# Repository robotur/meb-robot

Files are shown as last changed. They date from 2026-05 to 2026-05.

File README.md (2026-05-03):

# meb-robot
Retrospective documentation of a Maze Solver robot made for MEB ROBO 2025 &amp; 2026

This is a compact, autonomous maze solver robot. Made with a 3d printed chassis and IR sensors; was designed and iterated over the span of 2 years to optimize turning and wall following ability.

 * Microcontroller: Arduino Nano
 * Sensors: 3x MR 45-5V diffuse IR sensors
 * Custom 3D printed PETG
 * Logic: Wall following (Left side)
   
[Watch the video](https://youtu.be/hQ72KUeb8lM)

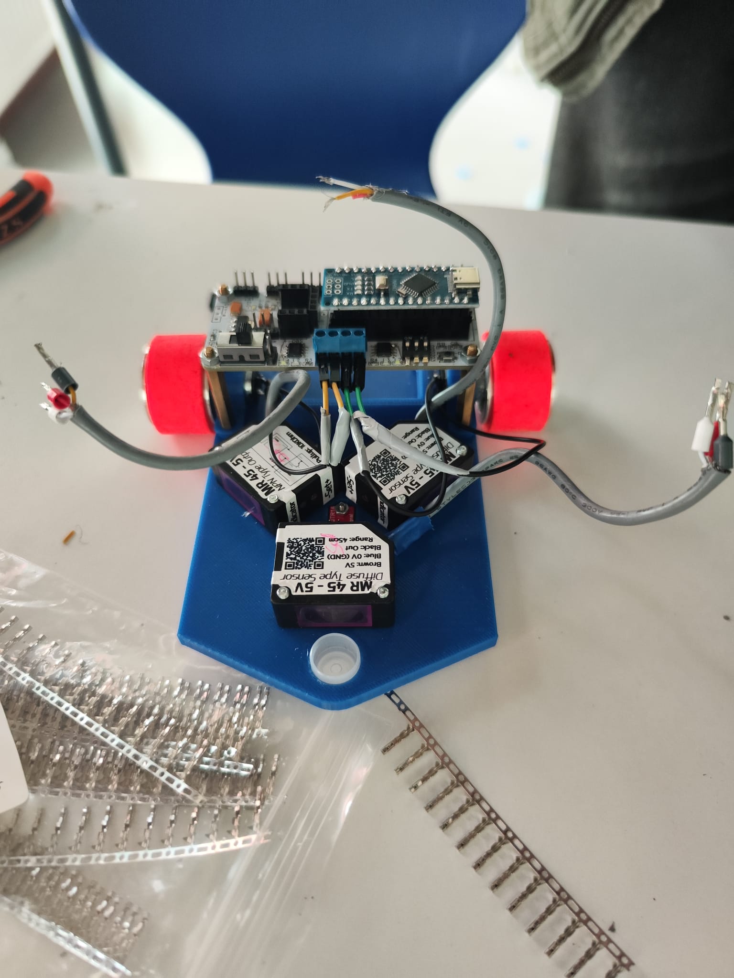
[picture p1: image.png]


# Engineering Decisions
Optimized sensor array for navigation:
 * used 3 point diffuse sensor array (45 degree angle to each side)
 * the 45 degree angle allows the sensors to detect the wall earlier allowing for smoother velocity transitions and preventing stuttering in logic

Finish detection:
 * used a compact QTR type IR sensor that faces the ground with a small mounting point in an accessible location in the middle of the chassis
 * this allows for a digital output signal showing whether the color of the ground is reflective or not (Effectively black/white) and thus allows me to find the differently colored finish grid

Inverted motor mount:
 * I mounted the motors on the top side of the chassis plate rather than the bottom
 * This lowers the entire chassis to the ground, lower CoM reduces the moment of inertia in high speed turns, massively decreasing the force that tips the robot/prevents it from losing traction

# Mentorship & Leadership
After a relatively successful 2025 season with 10 students (5 teams), there were a lot of interested students. I co-led the technical mentorship for 8 incoming Preparatory and 9th grade students.
I translated my 2025 and 2026 experience into a 'base model' (this repo) and i hope to enable new students and current participants to move past basic assembly and focus on more advanced logic and troubleshooting

 * Design and manufacturing: I handled the full CAD to print cycle, ensuring every team had a structurally sound chassis
 * Component Integration: I pre-selected the sensor array and motor positions to eliminate hardware level issues, allowing the students to focus on logic
 * Technical Direction: I gave them a guide to follow for connecting electronics components for optimal IO and logic management

By abstracting mechanical complexity I allowed the 8 junior students to engage directly with logic; turning raw signals into autonomous behavior through their own code.

# 2025-2026 Iteration Comparison
In the 2025 version, the motors were at the bottom of the plate. This meant the robot sat higher off the ground compared to other robots but also meant that because the caster wheel was shorter than the height of the chassis plate from the ground, it made the entire robot stand on a 15 degree angle which ruined the sensors' output because the sensors were effectively looking at the ground instead of forward.

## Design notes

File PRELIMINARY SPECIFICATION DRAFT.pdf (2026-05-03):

PRELIMINARY SPECIFICATION DRAFT

Challenge: During the integration phase, there was a hardware bottleneck. The three directional sensors and underside sensor and the motor drivers exhausted all available digital IO pins on the arduino nano.

Solution: I researched the ATmega328P silicon architecture and confirmed that pins A0 through A5 are internally mapped and can be addressed as digital pins using the “pinMode()” and “digitalRead()” functions

I instructed the students to solder 12 header pins (arranged in 4 signal-power-ground groups) onto the prototype shield, specifically utilizing the analog rail for digital input and pins for easy replacement incase of sensor failure

I guided the students through updating their code logic to treat A1-A5 as digital triggers successfully expanding our sensor capacity without needing a larger microcontroller

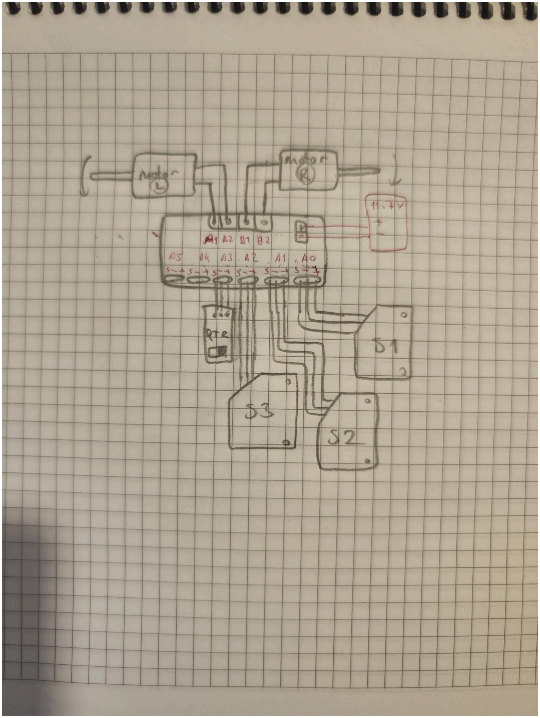
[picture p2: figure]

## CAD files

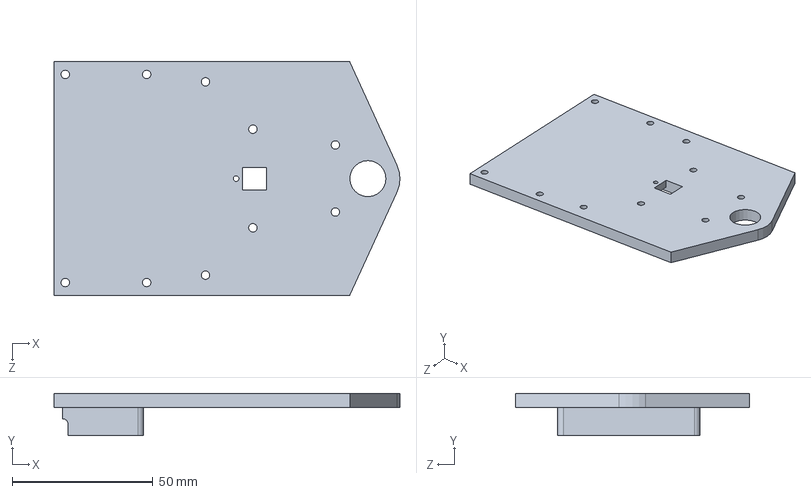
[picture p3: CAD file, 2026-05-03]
CAD/plate.SLDPRT
122.8 x 15.0 x 82.9 mm

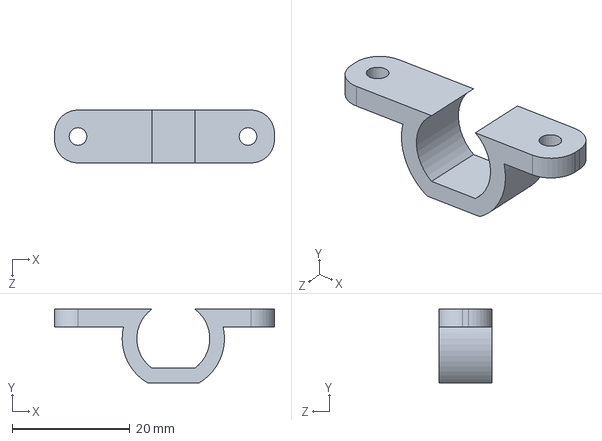
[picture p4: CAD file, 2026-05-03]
CAD/motor_holder.SLDPRT
37.4 x 12.5 x 9.00 mm

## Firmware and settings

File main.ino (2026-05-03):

// --- Hız Tanımlamaları ---
constexpr uint8_t DEFAULT_SPEED = 150;
constexpr uint8_t TURN_SPEED    = 100; 

// --- Motor Pin Tanımlamaları (T4950) ---
#define l_e_f_t_m_1 10
#define l_e_f_t_m_2 6
#define r_i_g_h_t_m_1 5
#define r_i_g_h_t_m_2 4

// --- MR45 Sensör Pinleri ---
#define SAG_SENSOR A1
#define SOL_SENSOR A3
#define ON_SENSOR  A2

void setup() {
  pinMode(l_e_f_t_m_1, OUTPUT);
  pinMode(l_e_f_t_m_2, OUTPUT);
  pinMode(r_i_g_h_t_m_1, OUTPUT);
  pinMode(r_i_g_h_t_m_2, OUTPUT);
  
  // MR45 Dijital veri gönderdiği için INPUT_PULLUP daha sağlıklı olabilir
  pinMode(SAG_SENSOR, INPUT);
  pinMode(SOL_SENSOR, INPUT);
  pinMode(ON_SENSOR,  INPUT);
}

void loop() {
  /* 
     MR45 MANTIĞI: 
     digitalRead == 0 -> ENGEL VAR
     digitalRead == 1 -> YOL BOŞ
  */
  bool solBos = digitalRead(SOL_SENSOR) == HIGH;
  bool onBos  = digitalRead(ON_SENSOR)  == HIGH;
  bool sagBos = digitalRead(SAG_SENSOR) == HIGH;

  // --- SOL ÖNCELİKLİ (Left Hand on Wall) ALGORİTMASI ---
  
  if (solBos) {
    // Solun boş olması en yüksek öncelik. 
    // Hafif ileri gidip öyle dönmek robotun duvara çarpmasını engeller.
    dur(); 
    delay(350); 
    solaDon();
    delay(200); // 90 derece tam dönene kadar ayarla
    ileriGit();
    delay(135);
  } 
  else if (onBos) {
    // Sol kapalıysa ama önün açıksa dümdüz devam et
    ileriGit();
  } 
  else if (sagBos) {
    // Sol ve ön kapalıysa sağa dön
    dur();
    delay(350);
    sagaDon();
    delay(200);
    ileriGit();
    delay(135);
  } 
  else {
    // Her yer kapalıysa 180 derece geri dön
    dur();
    delay(350);
    geriDon();
    delay(900); 
  }
}

// --- Hareket Fonksiyonları (T4950 Sürücü Yapısı) ---

void ileriGit() {
  analogWrite(l_e_f_t_m_1, DEFAULT_SPEED);
  digitalWrite(l_e_f_t_m_2, LOW);
  analogWrite(r_i_g_h_t_m_1, DEFAULT_SPEED);
  digitalWrite(r_i_g_h_t_m_2, LOW);
}

void solaDon() {
  digitalWrite(l_e_f_t_m_1, TURN_SPEED);
  analogWrite(l_e_f_t_m_2, LOW);   // Sol teker geri
  analogWrite(r_i_g_h_t_m_1,LOW); // Sağ teker ileri
  digitalWrite(r_i_g_h_t_m_2, TURN_SPEED);
}

void sagaDon() {
  analogWrite(l_e_f_t_m_1, LOW);   // Sol teker ileri
  digitalWrite(l_e_f_t_m_2, TURN_SPEED);
  digitalWrite(r_i_g_h_t_m_1, TURN_SPEED);
  analogWrite(r_i_g_h_t_m_2, LOW); // Sağ teker geri
}

void dur() {
  digitalWrite(l_e_f_t_m_1, LOW);
  digitalWrite(l_e_f_t_m_2, LOW);
  digitalWrite(r_i_g_h_t_m_1, LOW);
  digitalWrite(r_i_g_h_t_m_2, LOW);
}

void geriDon() {
  // 180 derece dönüş için sağa veya sola tam tur
  solaDon(); 
}
